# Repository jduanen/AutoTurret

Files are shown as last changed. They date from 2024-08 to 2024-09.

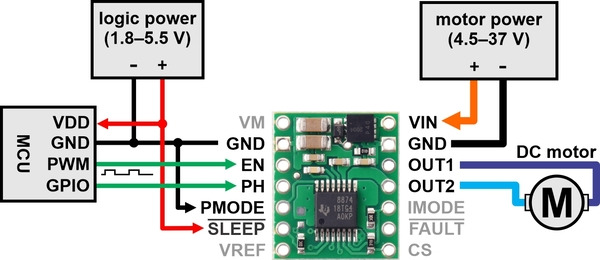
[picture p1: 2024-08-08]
imgs/DRV8876Pololu.jpg

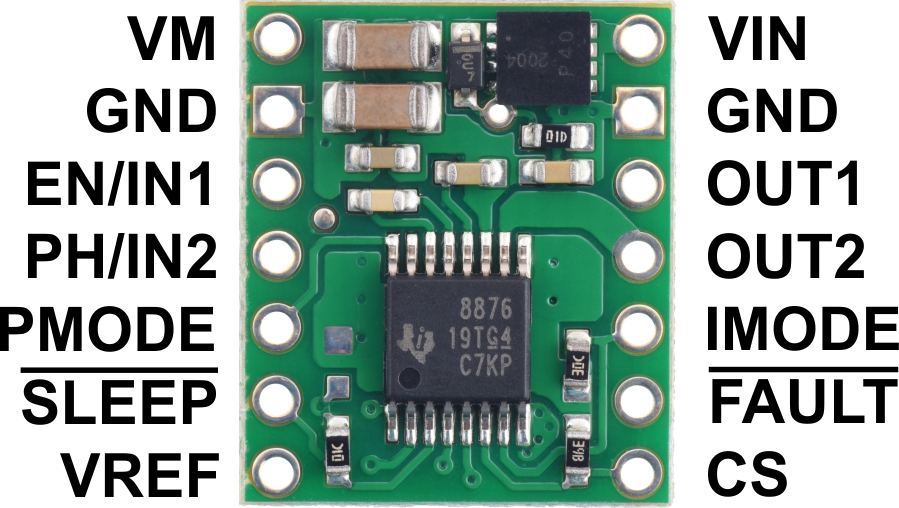
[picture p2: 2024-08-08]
imgs/PololuDRV8876.jpg

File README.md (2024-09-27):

# AutoTurret
An automated turret

## Features

* Servo-Driven Pan and Tilt Platform
  - ** TBD **

* Airsoft Armaments
  - Automatic Electric Gun (AEG)
    * for initial testing
    * ** TBD **
  - High-Pressure Air (HPA)
    * ** TBD **
  - High-Speed Feeder
    * requirements
      - <= 3000 pellets/min (50 pellets/sec)
      - no jamming over full capacity of pellets
      - sufficient capacity to match air supply
      - operates in all orientations (i.e., don't rely on gravity feed)
      - flexible feeder line
      - effective range <15 meters
      - ? J, ? fps
    * design features
      - ?
    * feeder data
      - 20V@?A: 44.5 p/s
        * max rate (24V@?A): 55 p/s
      - current limiting resistor for DRV8876
        * ? ohms: ????

* Sensors
  - Presence Detection
    * 24GHz radar
      - ** TBD **
    * PIR
      - ** TBD **
  - Vision-Based Detection
    * ** TBD **
  - Vision-Based Targeting
    * ** TBD **
  - Video Streaming
    * ** TBD **
  - Telemetry
    * ** TBD **
  - Airsoft Sensors
    * Chronograph
      - add pair of IR emitter/receiver pairs to tube added to end of barrel
        * make tube slightly larger than bore size
        * place emitter and receiver on opposite sides of the tube
        * separate emitter/receiver pairs by 50mm or 100mm
          - depends on achievable accuracy
        * ?
      - ?
    * Pellet Supply
      - <reference to model source>
        * <describe the mods I made>
        * <add cad files>
      - <flexible feeder tube>
      - 
    * Air Supply
      - ** TBD **
    * Orientation
      - absolute, repeatable, accurate (IMU, magnetometer)
      - ** TBD **

## Notes

* Test Environment
  - start with cheap AEG engine
    * remove from original plastic
    * design and print a new enclosure
  - create a test target
    * use 70mm cardboard shipping tube
    * add high-density foam with 45 degree face at far end
    * create a "plug" around the AEG barrel with high-density foam

* MOSFET AEG Trigger Circuit
  - put decoupling cap and back-EMF diode on AEG's DC motor
    * put them right on the motor terminals (avoid lead inductance)
  - MOSFET circuit
    * DC Motor connects between voltage source and Drain
    * Source connects to ground
    * pull-up resistor from Gate to motor voltage source to ensure it's turned on when trigger signal is high
    * maybe use the 20V supply voltage to run the AEG motor
      - if so, need to recalibrate firing rate
  - Motor supply must support high in-rush and high sustained current
  - use IRF540 because it has a lower Vth than the IRF520
  - 3.3V still isn't enough to fully saturate the IRF540
    * need to drive Gate to higher voltage (around 4.6V)
    * have to drive FET into saturation/low R
  - use 2N3904 to act as a level shifter from 3.3V input from controller to >5V output to Gate
  - RP2040 puts all GPIOs into HiZ state while loading (booting?)
    * need to make sure that the trigger doesn't activate during load/reboot
    * use pull-down resistor on input to level shifting transistor
  - 

* Chronograph
  - use ATmega328p
    * can also use ATmega2560, ATmega32U4, ATmega1284P
    * need TIMER1 16-bit timer/counter with external trigger
      - ATmega328P
        * Timer/Counter 0: 8-bit
        * Timer/Counter 1: 16-bit (with Input Capture capability)
        * Timer/Counter 2: 8-bit
      - ATmega2560
        * Timer/Counter 0: 8-bit
        * Timer/Counter 1: 16-bit (with Input Capture capability)
        * Timer/Counter 2: 8-bit
        * Timer/Counter 3: 16-bit (with Input Capture capability)
        * Timer/Counter 4: 16-bit (with Input Capture capability)
        * Timer/Counter 5: 16-bit (with Input Capture capability)
      - ATtiny84
        * Timer/Counter 0: 8-bit
        * Timer/Counter 1: 16-bit (with Input Capture capability)
    * use an Arduino Pro Mini 328 (Sparkfun-like clone)
      - https://www.sparkfun.com/products/11113
      - 18x33mm, 0.8mm thin PCB
      - power and status LEDs
      - Vin: 5-12VDC, 5V regulator, 150mA
      - 8x analog pins, 14x digital GPIOs
      - use FTDI USB to Serial converter
        * select 5V, also need to hook up DTR
    * use 5V version
      - for Arduino IDE: select Arduino Duemilanove
  - 12864 128x64 OLED display
    * 3-5V input (i/o is 5V tolerant)
    * SSD1306 controller
    * I2C interface, address: 0x3C
    * v1.1 is all white, -13 is yellow on top and blue below
      - 2x rows (32px) of yellow and 6x (96px) rows of blue
  - two sets of IR transmitter-receiver pairs
    * interrupt IR beam to mark start and end of pellet transit over fixed distance
    * pull up IR LED with 200 ohms to Vcc, and pull down via GPIO
      - Vcc=5V, Ilo=20mA, IR LED: 1.2V forward drop
    * IR photodiode
      - anode to Vcc
      - cathode to pull-down and GPIO input
      - 120K ohm pull-down resistor
    * IR emitter
      - anode to 180 ohm resistor to Vcc
      - cathode to GPIO output (ATmega328p can pull down 20mA)
  - calibration tests
    * distance between start and end sensors: 40mm
    * drop pellet from top of compression fitting (30mm from start sensor)
    * v = 1/2 * g * t^2
    * g = 9.8 m/s^2
    * d_1 = 30mm = 0.03 m
    * d_2 = 40mm = 0.04 m
    * t = sqrt((2 * d) / 9.8)
    * t_1 = sqrt((2 * 0.03) / 9.8) = 0.0782 secs
    * t_2 = sqrt((2 * (0.03 + 0.04)) / 9.8) = 0.1195 secs
    * t_d = (t_2 - t_1) = 0.0413 secs
    * v_avg = (d_2 / t_d) = (0.04 / 0.0413) = 0.9685 m/s
    * N.B. these numbers assume falling in a vacuum (and doesn't touch the walls)

* Pololu DRV8876 board
  - one motor channel
  - 1.3 A max continuous current (no heat sink)
  - adjustable current limiting
    * 2 A default
    * adjustable by pot/resistor across empty pads in bottom left of board
  - $6.95 (1 unit)
  - protection
    * under-voltage lockout
    * over-current and over-temperature
    * reverse-voltage
  - modes:
    * Phase/Enable (PH/EN): ?
    * PWM (IN/IN): ?
    * Independent half-bridge control: ?
  - logic voltage: 1.8-5.5 V
  - PWM input: <=100 kHz
  - pins
    * Current Sense (CS): analog output, 2500 mV/A
      - really noisy and have to either avg/filter or sample fast and avg
      --> not using this
    * Sleep (/SLEEP)
      - active low, put device to low-power sleep
      - starts up in sleep mode, logic high input brings out of sleep
      - takes Tsleep (1ms) to take effect
      - reads strapping pin states when in sleep mode
        * takes effect when coming out of sleep mode (rising edge of /SLEEP)
    * Motor Power (VIN): 4.5-37 V motor voltage input, reverse-voltage protected [use this]
    * Motor Voltage (VM): motor voltage after reverse-voltage protection
      - can use this to supply reverse-voltage protected voltage
      - need put decoupling caps on this
        --> already on the Pololu board
    * Operating Mode (PMODE):
      - 0/low: Phase/Enable mode, EN=PWM
        * PH=1: forward/brake at PWM% speed
        * PH=0: reverse/brake at PWM% speed
        * PH=PWM, EN=1/high
          - locked-antiphase mode
            * 0%: full speed in one direction
            * 50%: stop
            * 100%: full speed in the other direction
      - can do more advanced operations, but I'm using this mode
        * allows me to jog the feeder back and forth to help clear jams
    * OUT1/OUT2: goes to motor
    * Current Regulation and Protection Mode (IMODE)
      - four possible modes, based on state of pin
        * GND: fixed off-time, automatic retry, overcurrent only
        * 20K to GND: cycle-by-cycle, automatic retry, both current chopping and overcurrent
        * 62K to GND: cycle-by-cycle, outputs latched off, both current chopping and overcurrent
        * HiZ: fixed off-time, outputs latched off, overcurrent only
      - Overcurrent
        * disables outputs and enters a brake state for Toff time
          - in brake state both low-side MOSFETs are turned on
        * if EN or PH pins change during Toff:
          - exits Break state, resets and follows inputs again
        * Toff: 25 usec
        * Tdelay: 1.6 usec
      - Fixed Off-Time Current Chopping
        * can use 100% duty cycle in this mode
      - Cycle-by-Cycle Current Chopping
        * can't use 100% duty cycle in this mode
          - needs a new control input edge to exist Break state
        * pulls /FAULT pin low when chopping
      - Auto-Retry mode
        * if over-current for more than Tocp (3 usec)
          - disables MOSFETs and drives /FAULT low for Tretry (2 msec)
          - resets based on control inputs
            * resumes normal operation, repeats if still over-current
      - Latched-Off mode
        * disables MOSFETs, drives /FAULT low until reset
          - resets by /SLEEP pin or removing power (via VM)
    * Fault (/FAULT)
      - active low (open-drain), indicates over-current/-temperature
      - needs pull-up resistor (or PULLUP pin mode in Arduino)
        * 10K pullup works better than internal pull-up mode [don't know why]
      - just an indication, doesn't change operation
      - fault indicates current chopping if driving motor forward/reverse
        * otherwise its a device fault
        * if /FAULT=LOW and control inputs selecting hi-Z or slow-decay
          - then it's a device fault
  - need add a heat-sink as it gets hot
  - Tsleep: time to sleep from when nSleep=LOW

* Xiao RP2040
  - A0 values connected to CS (avg over 10 samples)
    * strong 2 KHz noise at slow speeds, to 1 KHz at full speed
      - this is the PWM frequency set in the test code
    * no load signal at different speeds (avg, voltage)
      - grounded: 0.3-0.4, n/a
      - 0%:   .7-.9, (Vmax=0mV,   Vmin=0mV,   Vavg=0mV)
      - 10%:  1-6,   (Vmax=222mV, Vmin=35mV,  Vavg=111mV)
      - 20%:  1-8,   (Vmax=275mV, Vmin=15mV,  Vavg=111mV)
      - 30%:  1-10,  (Vmax=315mV, Vmin=19mV,  Vavg=127mV)
      - 40%:  1-10,  (Vmax=356mV, Vmin=18mV,  Vavg=140mV)
      - 50%:  1-11,  (Vmax=375mV, Vmin=12mV,  Vavg=147mV)
      - 60%:  1-11,  (Vmax=371mV, Vmin=3mV,   Vavg=150mV)
      - 70%:  1-11,  (Vmax=356mV, Vmin=3mV,   Vavg=147mV)
      - 80%:  1-11,  (Vmax=318mV, Vmin=9mV,   Vavg=145mV)
      - 90%:  2-6,   (Vmax=272mV, Vmin=57mV,  Vavg=149mV)
      - 100%: 4-6,   (Vmax=208mV, Vmin=109mV, Vavg=150mV)
    * loaded: Vavg goes up significantly
    * CS reflects the PWM frequency
      - need to sample fast enough (>nyquist) to get good avg in SW
      - created a LPF with R=100K and C=.1uF to smooth the noise
    * 

* Airsoft data
  - Kinetic Energy: 1/2mv^2
      - 0.2g  6mm pellet at 400 FPS (122 m/s): 1.5 J
      - 0.2g  6mm pellet at 500 FPS (152 m/s): 2.3 J
      - 0.2g  6mm pellet at 600 FPS (183 m/s): 3.3 J
      - 0.25g 6mm pellet at 360 FPS (110 m/s): 1.5 J
      - 0.35g 6mm pellet at 450 FPS (137 m/s): 3.3 J
      - 0.4g  6mm pellet at 600 FPS (183 m/s): 6.7 J
  - Safety
    * energy levels
      - safe:   <2 J
      - strong: >2 J && <4 J
      - unsafe: >4 J
    * values in different regulations
      -    1.35 J: penetrating wound
      - 3.0-4.0 J: penetrating/leathal wound
      - 2.0-3.0 J: penetration level
    * human skin penetration (> 1/2 diameter of pellet)
      - 162.1e^(-0.38sqrt(m))
      - e.g., 0.2 g @ 136.7 m/s (448 FPS) -- possible with AEG
  - Velocity Range
    * AEG: 46-198 m/s (150-650 fps)
    * HPA: 55-226 m/s (180-740 fps); dynamically variable
  - Pellet Weights
    * 0.2-0.49 g
  - Rate of Fire (estimated max rate)
    * HPA: 2100-3600 pellets/min,   35-60 pellets/sec,  28.5-16.7 msec/pellet
    * AEG:  100-1500 pellets/min, 1.67-25 pellets/sec, 598.8-40.0 msec/pellet
  - Barrel Length
    * 221-430 mm
  - Distance between pellets in flight
    * ?
    * time through barrel: ?
  - AEG Piston-Barrel Volume Ratio
    * 2:1
  - Typical AEG
    * Velocity: 120 m/s (~400 fps)
    * Energy @ Distance
      - 1.4 J @  0 m
      -   1 J @  5 m
      - 0.6 J @ 10 m
      - 0.3 J @ 20 m
  - Ballistics
    * velocity drops exponentially with distance (due to the quadratic drag)
    * simple equation describes ideal (no hop-up, no wind) distance for given pellet diameter, weight, and speed
      - e.g., 6mm 0.2g 120m/s 1.8m height: hits ground at 34m

* Links
  - https://www.pololu.com/product/4036
  - https://www.pololu.com/product/4037
  - https://en.wikipedia.org/wiki/Airsoft_pellets
  -

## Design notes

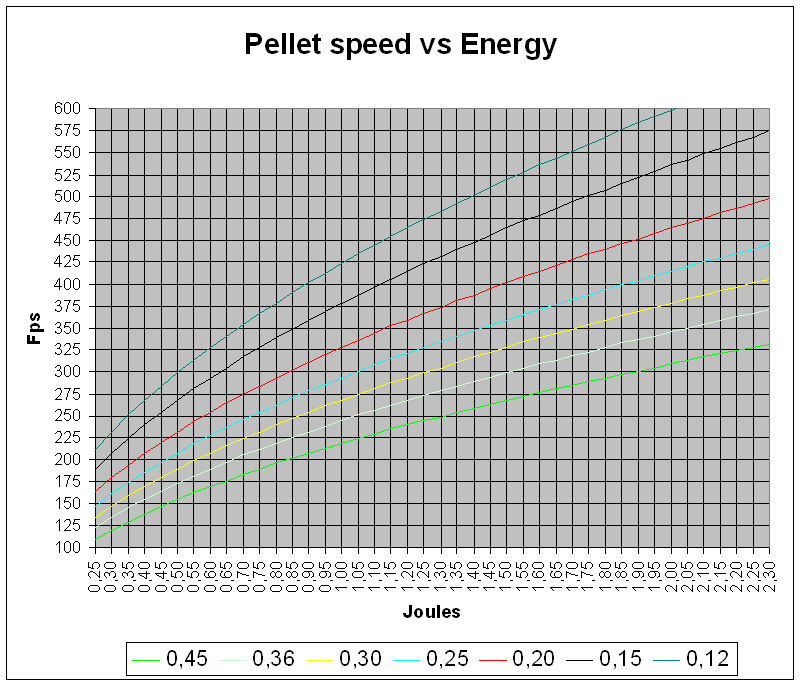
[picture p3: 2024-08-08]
imgs/Fps_vs_joules.jpeg

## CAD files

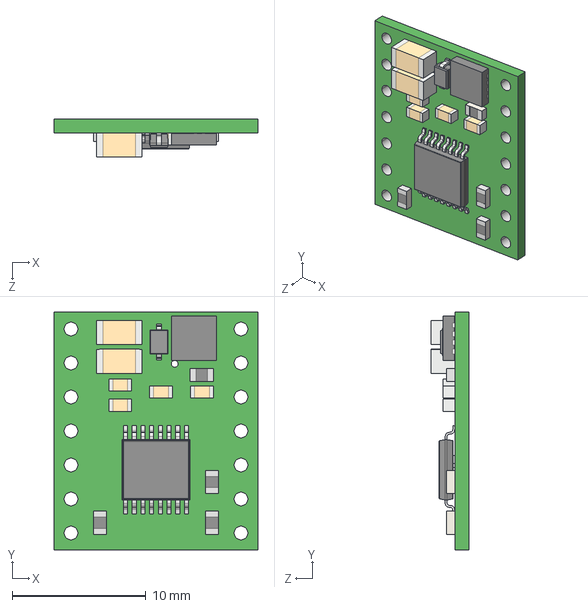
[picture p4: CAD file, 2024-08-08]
cad/drv887x-single-brushed-dc-motor-driver-carrier.step
15.2 x 17.8 x 2.82 mm

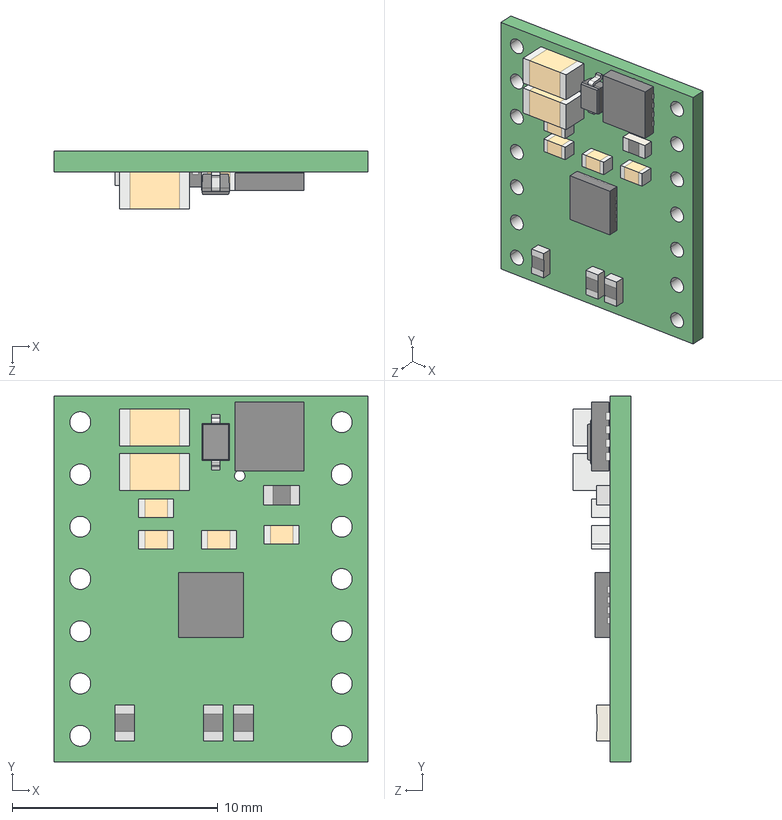
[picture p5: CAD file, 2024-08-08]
cad/drv8876-qfn-single-brushed-dc-motor-driver-carrier.step
15.2 x 17.8 x 2.82 mm

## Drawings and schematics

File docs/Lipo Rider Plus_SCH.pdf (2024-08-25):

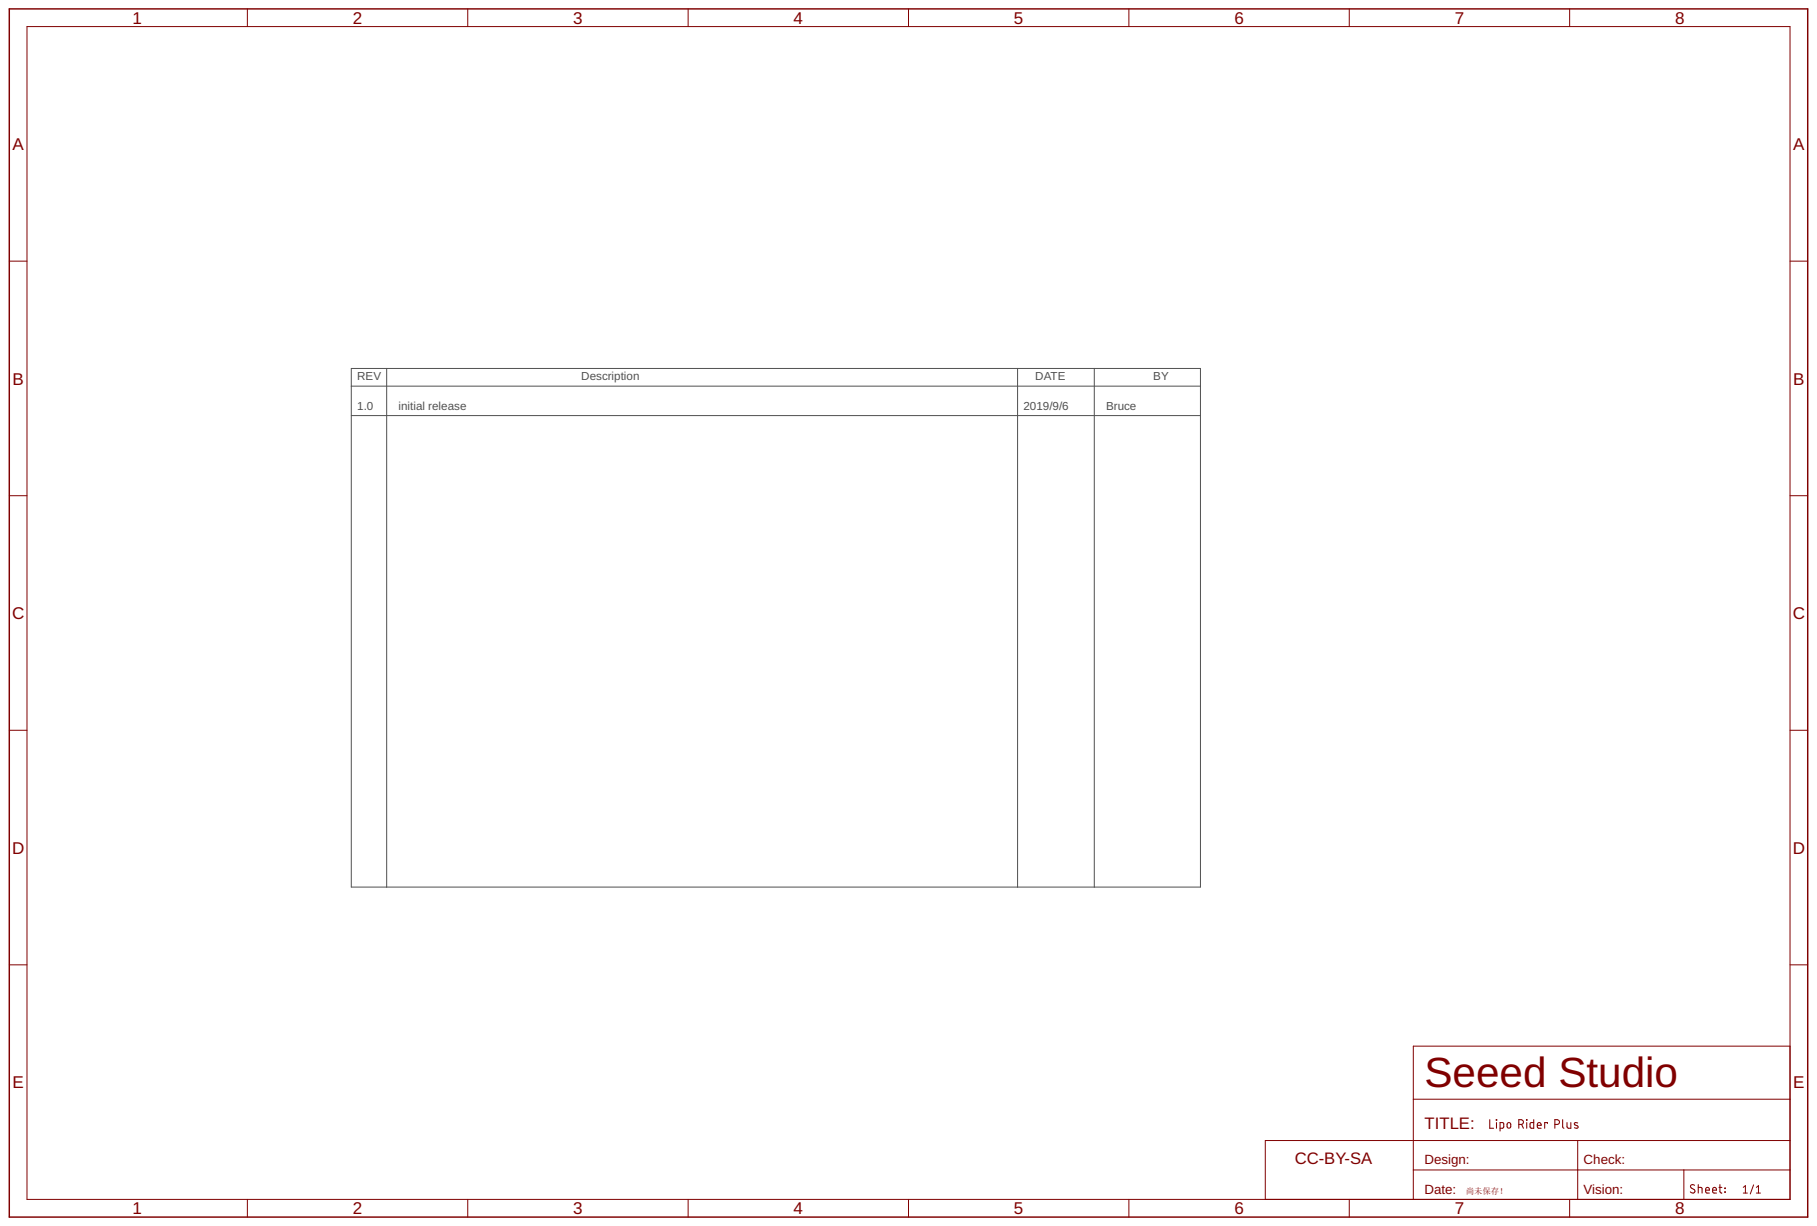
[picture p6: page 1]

TITLE: Design: | Check: Date: Vision: CC-BY-SA

尚未保存！

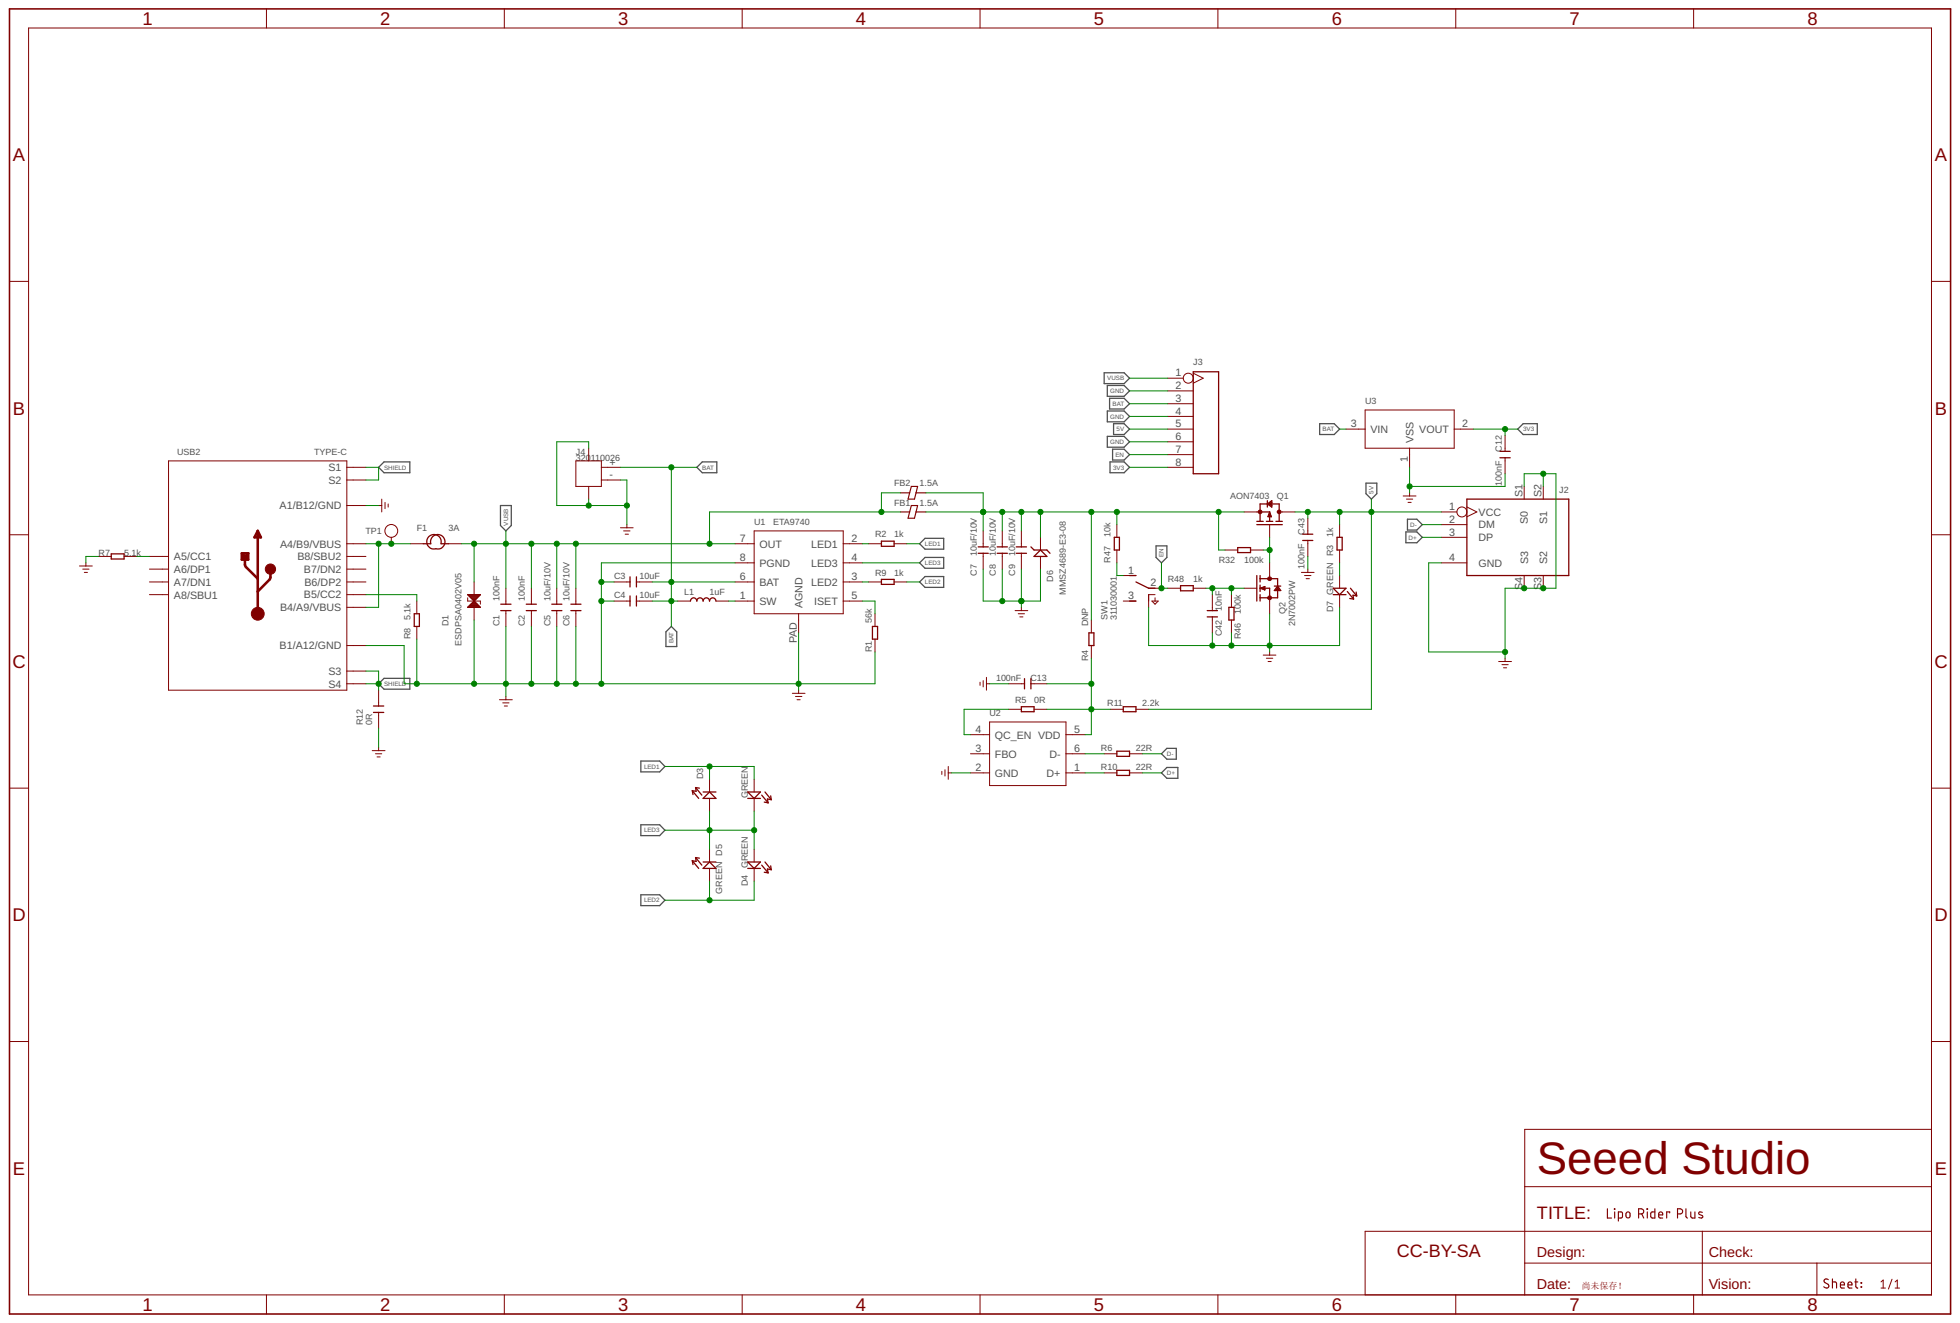
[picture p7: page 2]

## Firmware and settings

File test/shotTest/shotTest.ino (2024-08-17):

/******************************************************************************
 * 
 * AutoTurret test program
 * 
 ******************************************************************************/

#include <RP2040_PWM.h>
#include <cppQueue.h>

#include <OnBoardLED.h>


#define PWM_PIN         D3    // EN
#define DIR_PIN         D2    // PH
#define _SLEEP_PIN      D1    // _SLEEP
#define CS_PIN          A0    // CS
#define _FAULT_PIN      D10   // _FAULT
#define TRIG_PIN        D9

#define MIN_FREQ        500   // TODO fix this
#define MAX_FREQ        5000  // TODO fix this

// N.B. Shot Interval is in units of msec
#define MIN_SHOT_INTERVAL   150   // a function of the AEG and it's power supply
#define MAX_SHOT_INTERVAL   1000  // arbitrary value

// N.B. Shot Rate is shots/sec
#define MIN_SHOT_RATE       (1000.0 / MAX_SHOT_INTERVAL)  // 1 shot/sec
#define MAX_SHOT_RATE       (1000.0 / MIN_SHOT_INTERVAL)  // 6.67 shots/sec

// N.B. Duty Cycle is in % of motor speed
#define MIN_DUTY_CYCLE  30.0  // can't feed reliably below 30%
#define MAX_DUTY_CYCLE  99.99 // PWM not DC, so can't be 100%

// N.B. Feed Rate is in pellets/sec
#define MIN_FEED_RATE   15.4  // pellets/sec
#define MAX_FEED_RATE   55.6  // pellets/sec

#define PRIME_PELLETS   32    // a function of the length of the feeder tube

#define CMD_Q_SIZE      8


typedef enum CmdType_e {
  FIRE,
  CLEAR,
  FEED,
  TRIGGER,
  STOP
} CmdType;

typedef struct {
  CmdType cmd;
  uint32_t numShots;
  union {
    float shotRate;   // shots/sec
    float dutyCycle;  // %
  } data;
} ShotCmd_t;


bool primed;
float freq;
unsigned long feederTime;
unsigned long triggerTime;

RP2040_PWM *PWM_Instance;

OnBoardLED *neoPix;

cppQueue cmdQ(sizeof(ShotCmd_t), CMD_Q_SIZE, FIFO);


//// TODO make much of these functions inline/constexpr

constexpr float rateToDutyCycle(float shotRate) {
  return (1.742 * (shotRate * 1.81));
}

constexpr float dutyCycleToRate(float dutyCycle) {
  return ((0.574 * dutyCycle) - 1.81);
}

constexpr float normDutyCycle(float dutyCycle) {
  float dc;

  dc = (((dutyCycle > 0) && (dutyCycle < MIN_DUTY_CYCLE)) ? MIN_DUTY_CYCLE : dutyCycle);
  dc = ((dc > MAX_DUTY_CYCLE) ? MAX_DUTY_CYCLE : dc);

  if (dc != dutyCycle) {
    Serial.println("INFO: duty cycle normalized");
  }

  return dc;  // % of full motor speed
}

constexpr uint32_t normNumShots(uint32_t numShots) {
  uint32_t shots;

  shots = ((numShots < MIN_NUM_SHOTS) ? MIN_NUM_SHOTS : numShots);
  shots = ((shots > MAX_NUM_SHOTS) ? MAX_NUM_SHOTS : shots);

  if (shots != numShots) {
    Serial.println("INFO: number of shots normalized");
  }

  return shots;
}

constexpr float normShotRate(float shotRate) {
  float rate;

  rate = ((shotRate < MIN_SHOT_RATE) ? MIN_SHOT_RATE : shotRate);
  rate = ((rate > MAX_SHOT_RATE) ? MAX_SHOT_RATE : rate);

  if (rate != shotRate) {
    Serial.println("INFO: shot rate normalized");
  }

  return shotRate;  // shots/sec
}

void primeFeeder(uint32_t numPellets) {
  Serial.print("p: ");Serial.print(numPellets);Serial.print(", ");
  PWM_Instance->setPWM(PWM_PIN, freq, MAX_DUTY_CYCLE);
  delay(numPellets * MAX_FEED_RATE);
  Serial.println(numPellets * MAX_FEED_RATE);
  PWM_Instance->setPWM(PWM_PIN, freq, 0.0);
}

void fire(uint32_t numShots, float shotRate) {
  uint32_t duration;

  numShots = normNumShots(numShots);
  shotRate = normShotRate(shotRate);

  if (primed == false) {
    primeFeeder(PRIME_PELLETS);
    primed = true;
  }

  startTrigger(numShots, shotRate);
}

void startFeeder(uint32_t pellets, float shotRate) {
  unsigned long now = millis();

  //// FIXME select proper speed to do that many shots in the given time
  uint32_t duration = ?(shotRate);
  duration = ?

  float dutyCycle = MAX_DUTY_CYCLE;
//  dutyCycle = rateToDutyCycle(shotRate);
  dutyCycle = normDutyCycle(dutyCycle);
  PWM_Instance->setPWM(PWM_PIN, freq, dutyCycle);

  feederTime = now + duration;
}

void stopFeeder() {
  Serial.println("stopFeeder");
  PWM_Instance->setPWM(PWM_PIN, freq, 0.0);
  feederTime = 0;
}

void startTrigger(uint32_t numShots, float shotRate) {
  startFeeder(numShots, shotRate);

  //// TODO deal with min shot time
  unsigned long now = millis();
  uint32_t duration = ((numShots * 1000.0) / shotRate);  // msec
  triggerTime = now + duration;
  digitalWrite(TRIG_PIN, HIGH);
}

void stopTrigger() {
  Serial.println("stopTrigger");
  digitalWrite(TRIG_PIN, LOW);
  triggerTime = 0;
  stopFeeder();
}

// try to unjam the feeder by going back and forth a bit
void clearFeeder() {
  PWM_Instance->setPWM(PWM_PIN, freq, 0.0);
  digitalWrite(_SLEEP_PIN, LOW);
  delay(5);
  digitalWrite(_SLEEP_PIN, HIGH);

  digitalWrite(DIR_PIN, LOW);
  PWM_Instance->setPWM(PWM_PIN, freq, MAX_DUTY_CYCLE);
  delay(250);  //// TODO tune this value
  digitalWrite(DIR_PIN, HIGH);
  delay(250);  //// TODO tune this value
  PWM_Instance->setPWM(PWM_PIN, freq, 0.0);
}

void getInput(cppQueue *qPtr) {
  if (Serial.available()) {
    ShotCmd_t cmd;
    byte chr = Serial.peek();
    switch (chr) {
    case 'C':
    case 'c':
      cmd.cmd = CLEAR;
      break;
    case 'f':
      Serial.print("Fire: ");
      cmd.cmd = FIRE;
      cmd.numShots = Serial.parseFloat();
      cmd.data.shotRate = Serial.parseInt();
      Serial.print(cmd.numShots);Serial.print(", ");Serial.println(cmd.data.shotRate);Serial.flush();
      break;
    case 'o':
      Serial.println("Continuous");
      //// FIXME figure this one out
      cmd.cmd = FIRE;
      cmd.numShots = 1000000;
      cmd.data.shotRate = 5.0;  //// TODO figure out appropriate rate
      break;
    case 'p':
      Serial.println("Turn Feeder On");
      cmd.cmd = FEED;
      cmd.data.dutyCycle = Serial.parseFloat();
      break;
    case 's':
      Serial.println("Single Shot");Serial.flush();
      cmd.cmd = FIRE;
      cmd.numShots = 1;
      cmd.data.shotRate = 1.0;  //// TODO figure out appropriate rate
      break;
    default:
      Serial.println("Stop Shooting");
      cmd.cmd = STOP;
      break;
    }
    qPtr->push(&cmd);

    // flush the input
    while (Serial.available()) {
      Serial.read();
    }
  }
}

void setup() {
  Serial.begin(115200);
  while (!Serial) { ; };
  Serial.println("BEGIN");

  freq = 2000.0;  //// TODO figure out the right value for this
  primed = false;
  triggerTime = 0;

  // set up feeder motor controller
  pinMode(DIR_PIN, OUTPUT);
  digitalWrite(DIR_PIN, HIGH);
  pinMode(_SLEEP_PIN, OUTPUT);
  digitalWrite(_SLEEP_PIN, LOW);
  pinMode(CS_PIN, INPUT);  // ANALOG
  pinMode(_FAULT_PIN, INPUT); //, INPUT_PULLUP);
  digitalWrite(_SLEEP_PIN, HIGH);

  PWM_Instance = new RP2040_PWM(PWM_PIN, freq, 0.0);

  // set up trigger
  pinMode(TRIG_PIN, OUTPUT);
  digitalWrite(TRIG_PIN, LOW);

  // set up Neo Pixel
  neoPix = new OnBoardLED(NEOPIXEL_POWER, PIN_NEOPIXEL);
  neoPix->setColor(BLACK);

  Serial.println("START");Serial.flush();
}

void loop() {
  getInput(&cmdQ);
  if (cmdQ.isEmpty() == false) {
    float dutyCycle;
    ShotCmd_t cmd;
    cmdQ.pop(&cmd);
    switch (cmd.cmd) {
    case CLEAR:
      clearFeeder();
      break;
    case FIRE:
      fire(cmd.numShots, cmd.data.shotRate);
      break;
    case FEED:
      dutyCycle = normDutyCycle(cmd.data.dutyCycle);
      PWM_Instance->setPWM(PWM_PIN, freq, dutyCycle);
      break;
    case STOP:
      stopFeeder();
      stopTrigger();
      break;
    default:
      Serial.print("ERROR: invalid command type ("); Serial.print(cmd.cmd);Serial.println(")");
      break;
    }
  }

  unsigned long now = millis();  // N.B. rolls over after ~50 days of uptime
  //// TODO deal with rollover
  if (triggerTime && (triggerTime <= now)) {
    Serial.print(now);Serial.print(", ");Serial.println(triggerTime);
    stopTrigger();
  }

  if (digitalRead(_FAULT_PIN) == 0) {
    if (triggerTime) {
      neoPix->setColor(RED);  // fault while active
      digitalWrite(_SLEEP_PIN, LOW);
      delay(5);
      digitalWrite(_SLEEP_PIN, HIGH);
    } else {
      neoPix->setColor(MAGENTA);  // no fault while active
    }
  } else {
    neoPix->setColor(BLACK);  // no fault
  }
}

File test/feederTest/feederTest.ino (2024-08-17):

#include "RP2040_PWM.h"

#include <OnBoardLED.h>


#define PWM_PIN     D3    // EN
#define DIR_PIN     D2    // PH
#define _SLEEP_PIN  D1    // _SLEEP
#define CS_PIN      A0    // CS
#define _FAULT_PIN  D10   // _FAULT

#define MIN_DUTY_CYCLE  11.0
#define MAX_DUTY_CYCLE  99.9
#define MIN_FREQ        500


RP2040_PWM *PWM_Instance;
OnBoardLED *neoPix;

float freq = 2000;
float dutyCycle = 0.0;
unsigned long lastTime = millis();
unsigned long loopCnt = 0;
float currentSense = 0;


// try to unjam the feeder by going back and forth a bit
void clearFeeder() {
  PWM_Instance->setPWM(PWM_PIN, freq, 0.0);
  digitalWrite(_SLEEP_PIN, LOW);
  delay(5);
  digitalWrite(_SLEEP_PIN, HIGH);

  digitalWrite(DIR_PIN, LOW);
  PWM_Instance->setPWM(PWM_PIN, freq, MAX_DUTY_CYCLE);
  delay(250);  //// TODO tune this value
  digitalWrite(DIR_PIN, HIGH);
  delay(250);  //// TODO tune this value
  PWM_Instance->setPWM(PWM_PIN, freq, 0.0);
}

void checkInput() {
  byte cmd;
  uint32_t duration;

  if (Serial.available()) {
    cmd = Serial.peek();
    switch (cmd) {
    case 'C':
    case 'c':
      Serial.println("Clear");
      clearFeeder();
      break;
    case 'S':
      // start max speed
      dutyCycle = MAX_DUTY_CYCLE;
      PWM_Instance->setPWM(PWM_PIN, freq, dutyCycle);
      Serial.println("Start");
      break;
    case 'f':
      // set frequency
      freq = Serial.parseFloat();
      freq = (freq < MIN_FREQ) ? MIN_FREQ : freq;
      PWM_Instance->setPWM(PWM_PIN, freq, dutyCycle);
      Serial.print("Freq: "); Serial.println(freq);
      break;

      dutyCycle = Serial.parseFloat();
      if (dutyCycle < MIN_DUTY_CYCLE) {
        dutyCycle = 0.0;
      } else if (dutyCycle >= 100.0) {
        dutyCycle = MAX_DUTY_CYCLE;
      }
      PWM_Instance->setPWM(PWM_PIN, freq, dutyCycle);
      Serial.print("Speed: "); Serial.println(dutyCycle);
      break;
    case 'x':
      dutyCycle = Serial.parseFloat();
      if (dutyCycle < MIN_DUTY_CYCLE) {
        dutyCycle = 0.0;
      } else if (dutyCycle >= 100.0) {
        dutyCycle = MAX_DUTY_CYCLE;
      }
      duration = Serial.parseInt();

      Serial.print("Duty Cycle: "); Serial.print(dutyCycle);
      Serial.print(", Duration: "); Serial.print(duration);
      Serial.println(" (msec)");
      PWM_Instance->setPWM(PWM_PIN, freq, dutyCycle);
      delay(duration);
      PWM_Instance->setPWM(PWM_PIN, freq, 0);
      break;
    default:
      // stop
      dutyCycle = 0.0;
      PWM_Instance->setPWM(PWM_PIN, freq, dutyCycle);
      Serial.println("Stop");
      break;
    }

    // flush the input
    while (Serial.available()) {
      Serial.read();
    }
  }
}

void setup() {
  Serial.begin(115200);
  while (!Serial) { ; };
  Serial.println("BEGIN");

  pinMode(DIR_PIN, OUTPUT);
  pinMode(_SLEEP_PIN, OUTPUT);
  pinMode(CS_PIN, INPUT);  // ANALOG
  pinMode(_FAULT_PIN, INPUT_PULLUP);

  digitalWrite(_SLEEP_PIN, LOW);
  digitalWrite(DIR_PIN, HIGH);

  PWM_Instance = new RP2040_PWM(PWM_PIN, freq, dutyCycle);
  PWM_Instance->setPWM(PWM_PIN, freq, dutyCycle);
  Serial.print("Initial Duty Cycle: ");Serial.println(dutyCycle);

  neoPix = new OnBoardLED(NEOPIXEL_POWER, PIN_NEOPIXEL);
  neoPix->setColor(BLACK);

  digitalWrite(_SLEEP_PIN, HIGH);
  Serial.println("START");
}

void loop() {
  checkInput();

  if (dutyCycle > MIN_DUTY_CYCLE) {
    if (digitalRead(_FAULT_PIN) == 0) {
      neoPix->setColor(RED);
    } else {
      neoPix->setColor(GREEN);
    }
  } else {
    neoPix->setColor(BLACK);
  }

  loopCnt++;
}

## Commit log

2024-08-08 First cut at working test.
2024-08-11 Fixed delay time between shots.
    [triggerTest.ino]
2024-08-15 Converted to millis()-based.
2024-08-25 Added IR LED enable/disable.
2024-08-28 Added input button stub.
2024-08-28 Fixed on-board LED. Fixed detector inputs.
    [chronoTest.ino]
2024-08-29 Removed on-board LED.
2024-09-27 Added units startup option. Velocity float print.
